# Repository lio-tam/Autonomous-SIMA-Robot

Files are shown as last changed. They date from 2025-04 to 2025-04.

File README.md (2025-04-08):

# Autonomer Roboter mit STM32
Dieses Projekt entstand im Rahmen meines Studiums an der RWTH Aachen. Ziel war es, einen Roboter zu bauen, der autonom einfache Bewegungen ausführt.

## Funktionen
- Eigenes Design der Steuerplatine mit KiCad
- Manuelle Bestückung & SMD-Löten
- Firmware in C für STM32
- Nutzung von Modm zum Flashen
- Projektplanung mit Gantt

## Verwendete Technologien
- STM32CubeIDE
- KiCad
- modm
- Logic Analyzer, CoolTerm

## Herausforderungen
- Fehlersuche bei Signalverlusten
- Austausch defekter Komponenten
- Zeitmanagement & Teamkoordination

## Medien
<div style="border:1px solid #ccc; border-radius:8px; padding:16px; margin:16px 0; box-shadow:2px 2px 6px rgba(0,0,0,0.1);">
  <h3 style="margin-top:12px;">Steuerplatine (Top View)</h3>
  <p>Die Oberseite der selbst entwickelten Steuerplatine – entworfen mit KiCad und per Hand bestückt.</p>
  driver-bild
</div>

<div style="border:1px solid #ccc; border-radius:8px; padding:16px; margin:16px 0; box-shadow:2px 2px 6px rgba(0,0,0,0.1);">
  <h3 style="margin-top:12px;">3D-Ansicht der Platine</h3>
  <p>Das mit KiCad erzeugte 3D-Modell zeigt die geplante Bestückung und Bauteilausrichtung.</p>
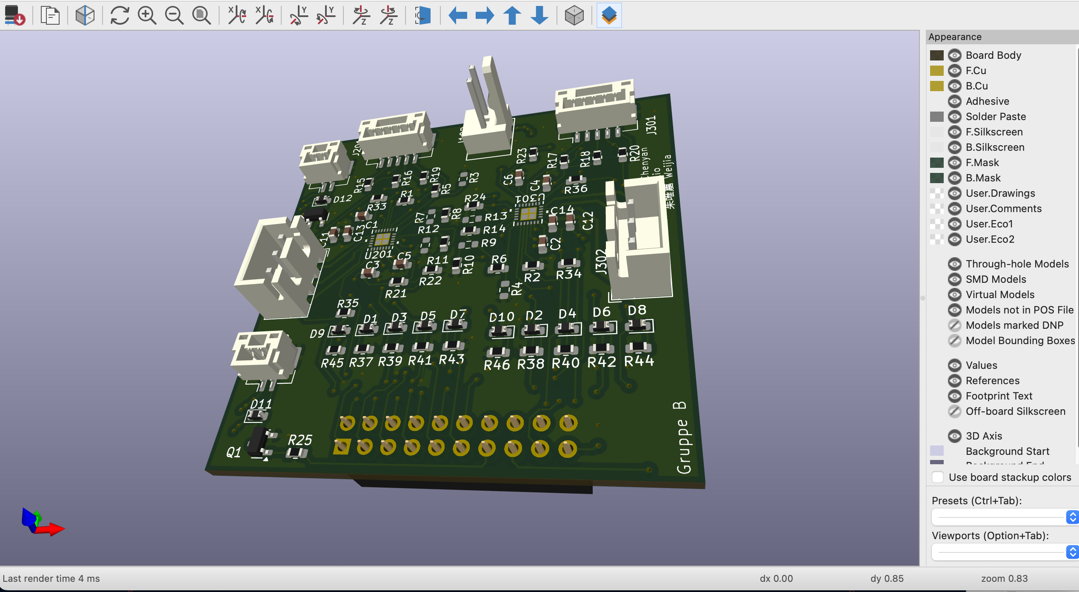
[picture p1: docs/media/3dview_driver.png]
3D-Ansicht
  
</div>

<div style="border:1px solid #ccc; border-radius:8px; padding:16px; margin:16px 0; box-shadow:2px 2px 6px rgba(0,0,0,0.1);">
  <h3 style="margin-top:12px;">Schaltplanansicht der Platine</h3>
  <p>Sie diente dazu, die Schaltungen zu planen und so anzuordnen, dass die Bauteile kompakt und effizient auf der Platine positioniert werden konnten.</p>
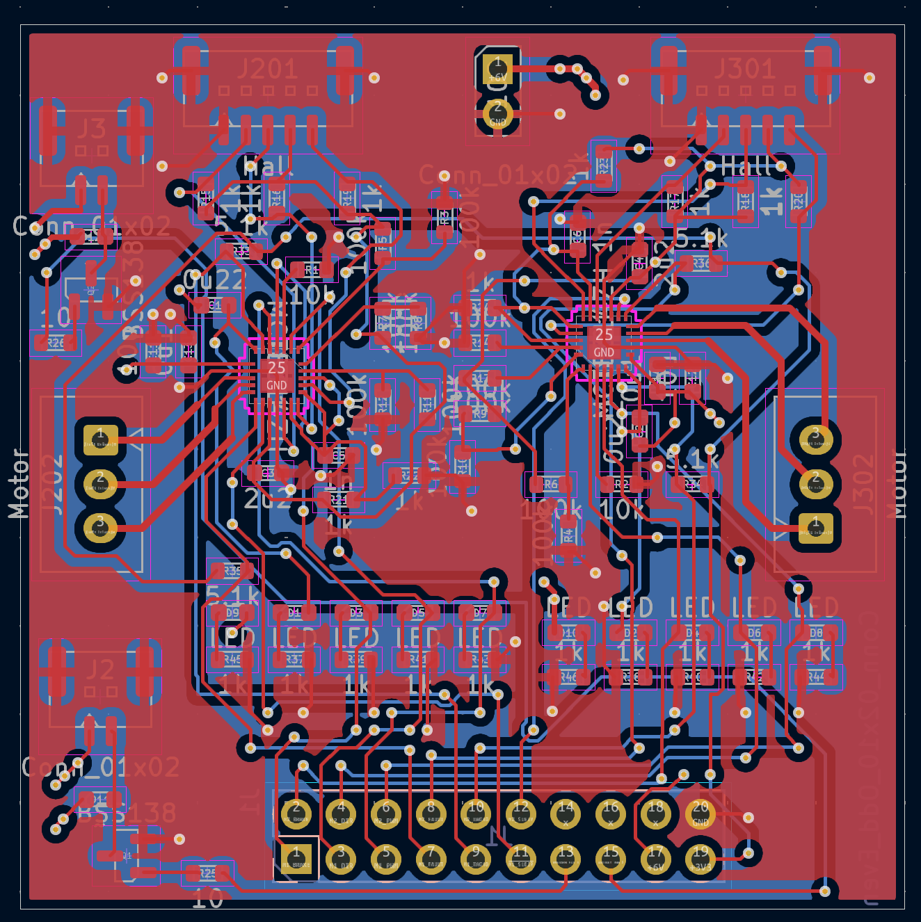
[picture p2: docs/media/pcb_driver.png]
Bestückte Platine
  
</div>

<div style="border:1px solid #ccc; border-radius:8px; padding:16px; margin:16px 0; box-shadow:2px 2px 6px rgba(0,0,0,0.1);">
  <h3 style="margin-top:12px;">Schaltplan – linker Teil</h3>
  <p>Ein Ausschnitt des Schaltplans mit Fokus auf die Spannungsversorgung und Mikrocontroller-Anbindung.</p>
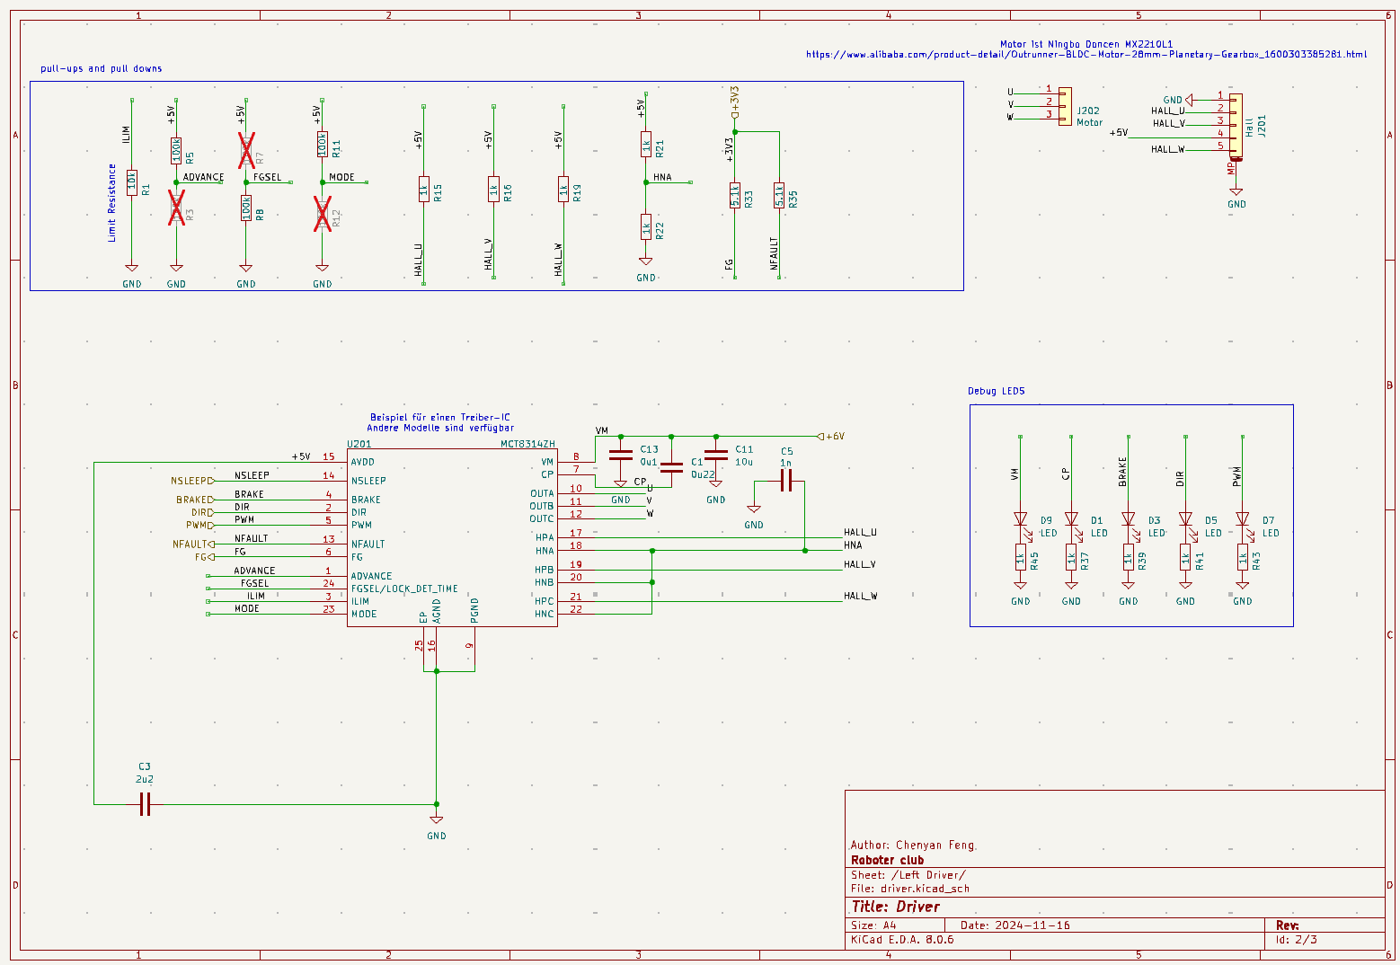
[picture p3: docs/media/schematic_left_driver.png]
Schaltplan (links)
  
</div>

<div style="border:1px solid #ccc; border-radius:8px; padding:16px; margin:16px 0; box-shadow:2px 2px 6px rgba(0,0,0,0.1);">
  <h3 style="margin-top:12px;">Firmware-Upload via SIMA</h3>
  <p>Flashing der Firmware über Modm – der Roboter wird mit neuer Software bespielt.</p>
  SIMA Flashing
</div>

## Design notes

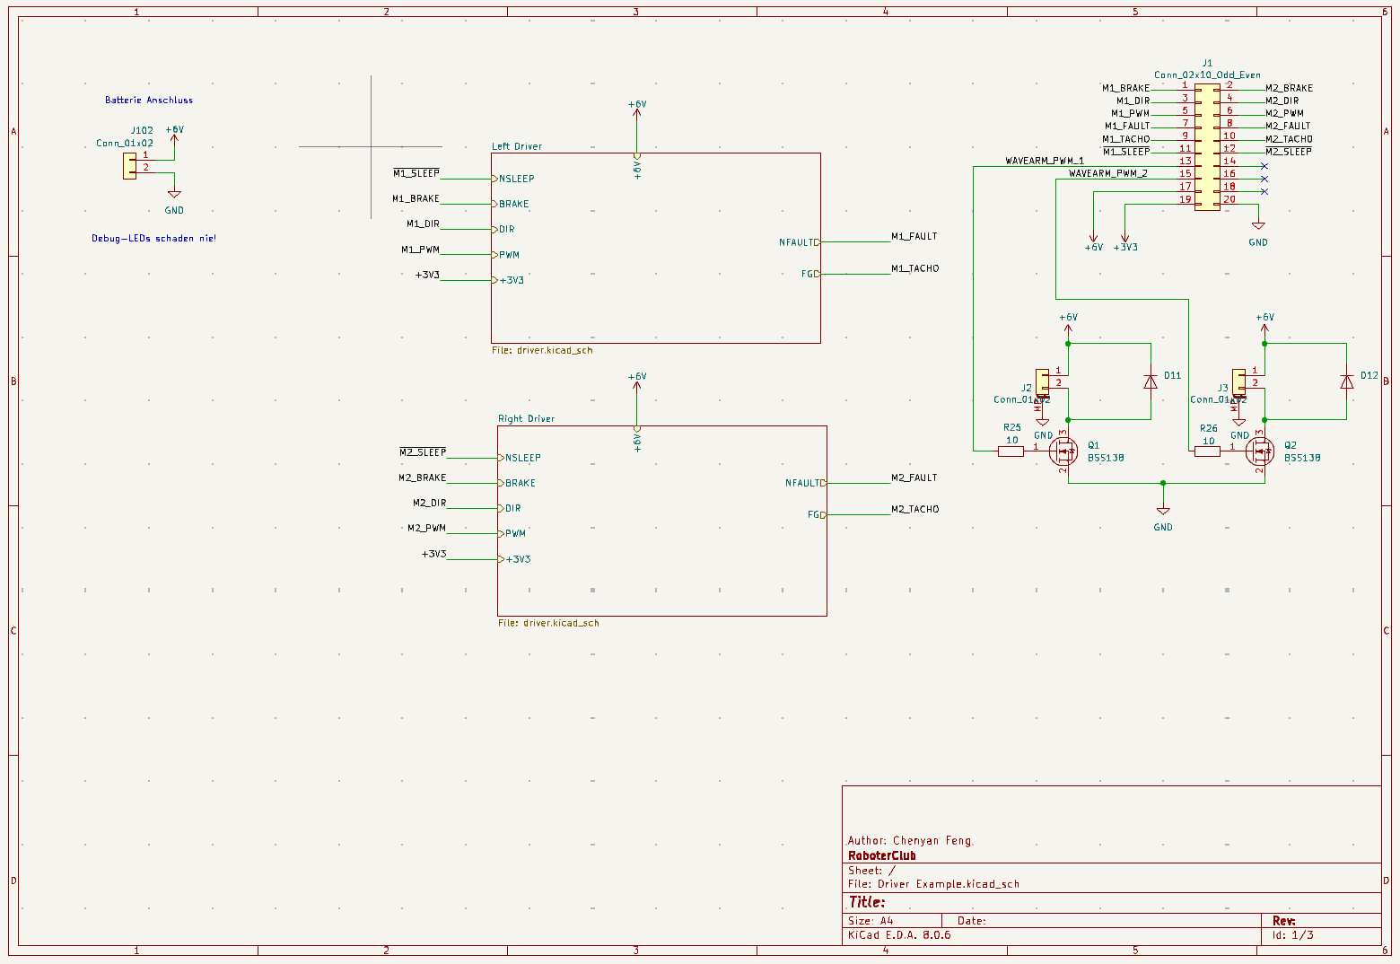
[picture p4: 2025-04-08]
docs/media/schematic_driver.png

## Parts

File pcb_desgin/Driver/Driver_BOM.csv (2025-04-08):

Reference | Value | Datasheet | Footprint | Name | Qty | Link | Preis | Gesamtpreis
C1;C2 | 0u22 | https://product.tdk.com/system/files/dam/doc/product/capacitor/ceramic/mlcc/catalog/mlcc_commercial_general_en.pdf | Capacitor_SMD:C_0603_1608Metric | C1608X5R1E224K080AA | 2 | https://www.digikey.de/de/products/detail/tdk-corporation/C1608X5R1E224K080AA/2093408 | 0,10 €
C3;C4 | 2u2 | https://mm.digikey.com/Volume0/opasdata/d220001/medias/docus/421/CL10A225KO8NNNC_Spec.pdf | Capacitor_SMD:C_0603_1608Metric | CL10A225KO8NNNC | 2 | https://www.digikey.de/de/products/detail/samsung-electro-mechanics/CL10A225KO8NNNC/3886698 | 0,08 €
C5;C6 | 1n | ~ | Capacitor_SMD:C_0603_1608Metric | CGA3E2X7R1H102K080DA | 2 | https://www.digikey.de/de/products/detail/tdk-corporation/CGA3E2X7R1H102K080DA/22106087 | 0,10 €
C11;C12 | 10u | ~ | Capacitor_SMD:C_0603_1608Metric | CL10A106KQ8NNNC | 2 | https://www.digikey.de/de/products/detail/samsung-electro-mechanics/CL10A106KQ8NNNC/3886696 | 0,10 €
C13;C14 | 0u1 | ~ | Capacitor_SMD:C_0603_1608Metric | TMK107BJ104KA-T | 2 | https://www.digikey.de/de/products/detail/taiyo-yuden/TMK107BJ104KA-T/930597 | 0,08 €
D1;D2;D3;D4;D5;D6;D7;D8;D9;D10 | LED | ~ | Diode_SMD:D_0603_1608Metric | 150060VS75000 | 10 | https://www.digikey.de/de/products/detail/w%C3%BCrth-elektronik/150060VS75000/4489906 | 0,13 €
D11;D12 | ~ | ~ | Diode_SMD:D_0603_1608Metric | VSKY20301608-G4-08 | 2 | https://www.digikey.de/de/products/detail/vishay-general-semiconductor-diodes-division/VSKY20301608-G4-08/6605119 | 0,48 €
J1 | Conn_02x10_Odd_Even | ~ | Connector_PinSocket_2.54mm:PinSocket_2x10_P2.54mm_Vertical | FHMD-DA020G1NBON-B | 1 | https://www.digikey.de/en/products/detail/superior-tech/FHMD-DA020G1NBON-B/16583446 | 0,69 €
J2;J3 | Conn_01x02 | ~ | Connector_JST:JST_GH_BM02B-GHS-TBT_1x02-1MP_P1.25mm_Vertical | BM02B-GHS-TBT | 2 | https://www.digikey.de/en/products/detail/jst-sales-america-inc/BM02B-GHS-TBT/807800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 | 0,31 €
J102 | Conn_01x02 | ~ | custom_footprints:2-Pin_PSK |  | 1
J201;J301 | Hall | ~ | Connector_JST:JST_GH_BM05B-GHS-TBT_1x05-1MP_P1.25mm_Vertical | BM05B-GHS-TBT | 2 | https://www.digikey.de/en/products/detail/jst-sales-america-inc/BM05B-GHS-TBT/807803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 | 0,39 €
J202;J302 | Motor | ~ | Connector_JST:JST_XH_B3B-XH-A_1x03_P2.50mm_Vertical | B3B-XH-A | 2 | https://www.digikey.de/en/products/detail/jst-sales-america-inc/B3B-XH-A(LF)(SN)/1651046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 | 0,12 €
Q1;Q2 | BSS138 | https://www.onsemi.com/pub/Collateral/BSS138-D.PDF | Package_TO_SOT_SMD:SOT-23 | BSS138 | 2 | https://www.digikey.de/de/products/detail/onsemi/BSS138/244210 | 0,26 €
R1;R2 | 10k | ~ | Resistor_SMD:R_0603_1608Metric | RMCF0603JT10K0 | 2 | https://www.digikey.de/de/products/detail/stackpole-electronics-inc/RMCF0603JT10K0/1758104 | 0,10 €
R3;R4;R7;R9;R12;R14 | 100k | ~ | Resistor_SMD:R_0603_1608Metric | ERJ-2RKF1003X | 6 | https://www.digikey.de/de/products/detail/panasonic-electronic-components/ERJ-2RKF1003X/192081 | 0,10 €
R5;R6;R8;R10;R11;R13 | 100k | ~ | Resistor_SMD:R_0603_1608Metric | ERJ-2RKF1003X | 6 | https://www.digikey.de/de/products/detail/panasonic-electronic-components/ERJ-2RKF1003X/192081 | 0,10 €
R15;R16;R17;R18;R19;R20;R21;R22;R23;R24;R37;R38;R39;R40;R41;R42;R43;R44;R45;R46 | 1k | ~ | Resistor_SMD:R_0603_1608Metric | ERJ-2RKF1001X | 20 | https://www.digikey.de/de/products/detail/panasonic-electronic-components/ERJ-2RKF1001X/79729 | 0,10 €
R25;R26 | 10 | ~ | Resistor_SMD:R_0603_1608Metric | ERJ-2RKF10R0X | 2 | https://www.digikey.de/de/products/detail/panasonic-electronic-components/ERJ-2RKF10R0X/192072 | 0,10 €
R33;R34;R35;R36 | 5.1k | ~ | Resistor_SMD:R_0603_1608Metric | ERA-2AEB512X | 4 | https://www.digikey.de/de/products/detail/panasonic-electronic-components/ERA-2AEB512X/1706022 | 0,17 €
U201;U301 | MCT8314ZH | https://www.ti.com/product/MCT8314Z | custom_footprints:WQFN24_RRW_TEX_new |  | 2

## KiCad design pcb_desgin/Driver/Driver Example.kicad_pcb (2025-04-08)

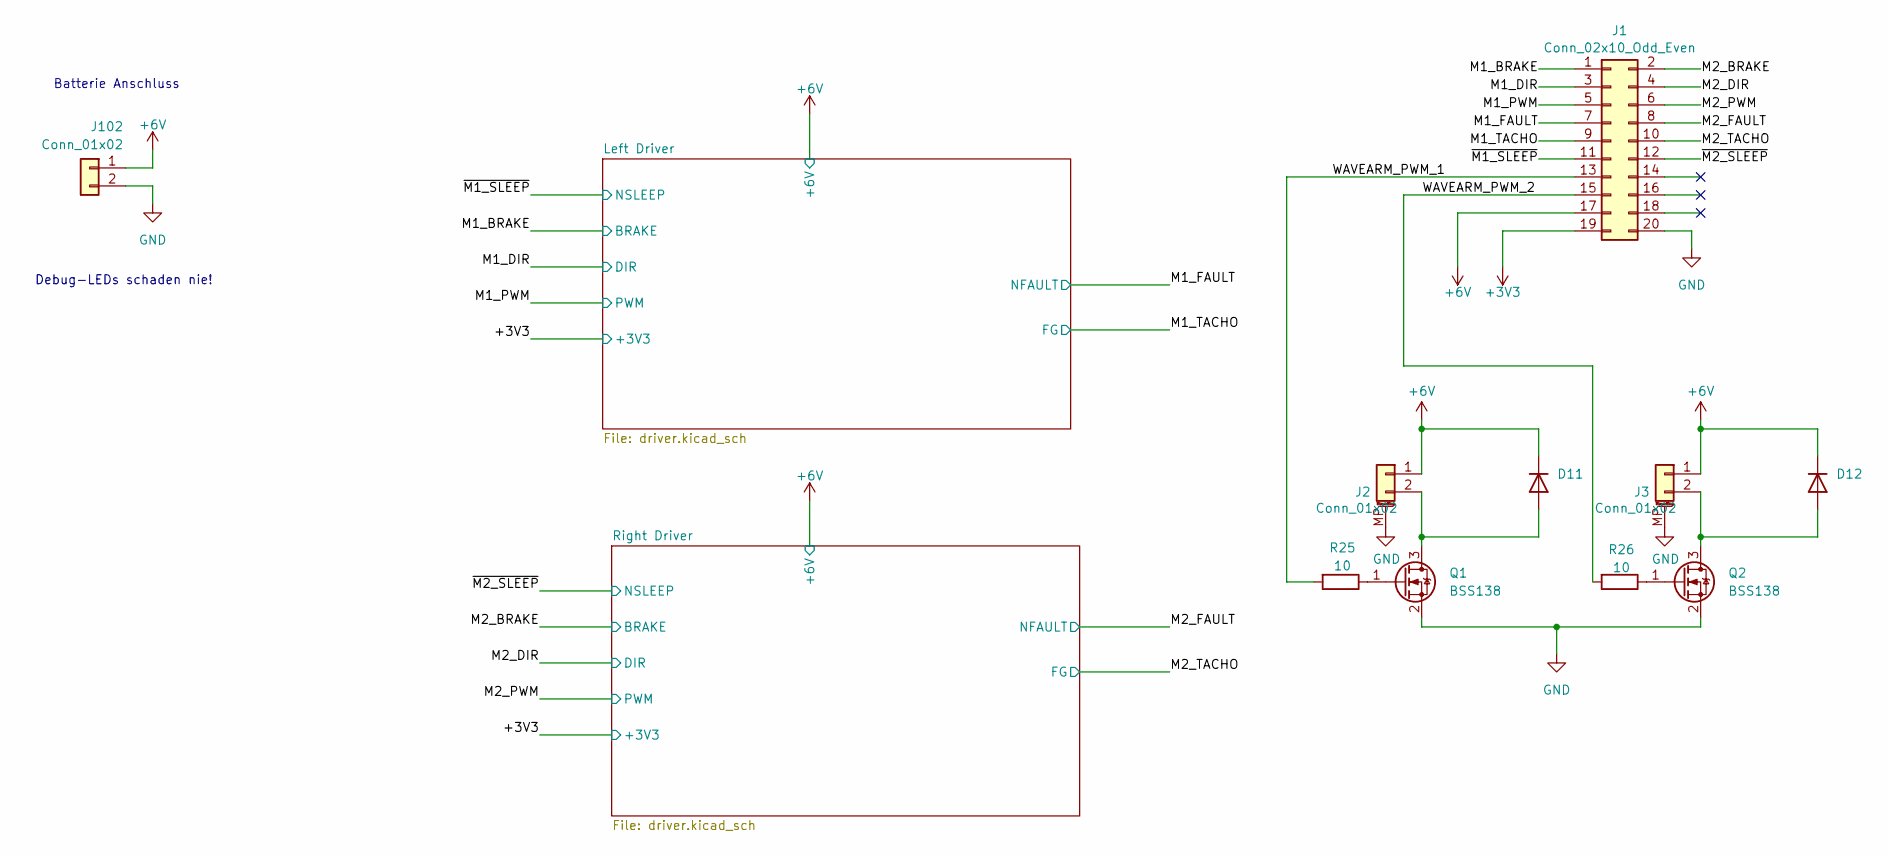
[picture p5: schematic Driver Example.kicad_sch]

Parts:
D11, D12: D_0603_1608Metric
J1: Conn_02x10_Odd_Even; PinSocket_2x10_P2.54mm_Vertical
J2, J3: Conn_01x02; JST_GH_BM02B-GHS-TBT_1x02-1MP_P1.25mm_Vertical
J102: Conn_01x02; 2-Pin_PSK
Q1, Q2: BSS138; SOT-23
R25, R26: 10; R_0603_1608Metric

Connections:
+3V3: J1.19; also elsewhere on the board
+6V: D11.1 (K), D12.1 (K), J1.17, J2.1, J3.1, J102.1; also elsewhere on the board
/M1_BRAKE: J1.1; also elsewhere on the board
/M1_DIR: J1.3; also elsewhere on the board
/M1_FAULT: J1.7; also elsewhere on the board
/M1_PWM: J1.5; also elsewhere on the board
/M1_TACHO: J1.9; also elsewhere on the board
/M2_BRAKE: J1.2; also elsewhere on the board
/M2_DIR: J1.4; also elsewhere on the board
/M2_FAULT: J1.8; also elsewhere on the board
/M2_PWM: J1.6; also elsewhere on the board
/M2_TACHO: J1.10; also elsewhere on the board
/WAVEARM_PWM_1: J1.13, R25.2
/WAVEARM_PWM_2: J1.15, R26.2
/~M1_SLEEP: J1.11; also elsewhere on the board
/~M2_SLEEP: J1.12; also elsewhere on the board
GND: J1.20, J2.MP (MountPin), J3.MP (MountPin), J102.2, Q1.2 (S), Q2.2 (S); also elsewhere on the board
unnamed: D11.2 (A), J2.2, Q1.3 (D)
unnamed: D12.2 (A), J3.2, Q2.3 (D)
unnamed: Q1.1 (G), R25.1
unnamed: Q2.1 (G), R26.1

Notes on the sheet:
Debug-LEDs schaden nie!
Batterie Anschluss

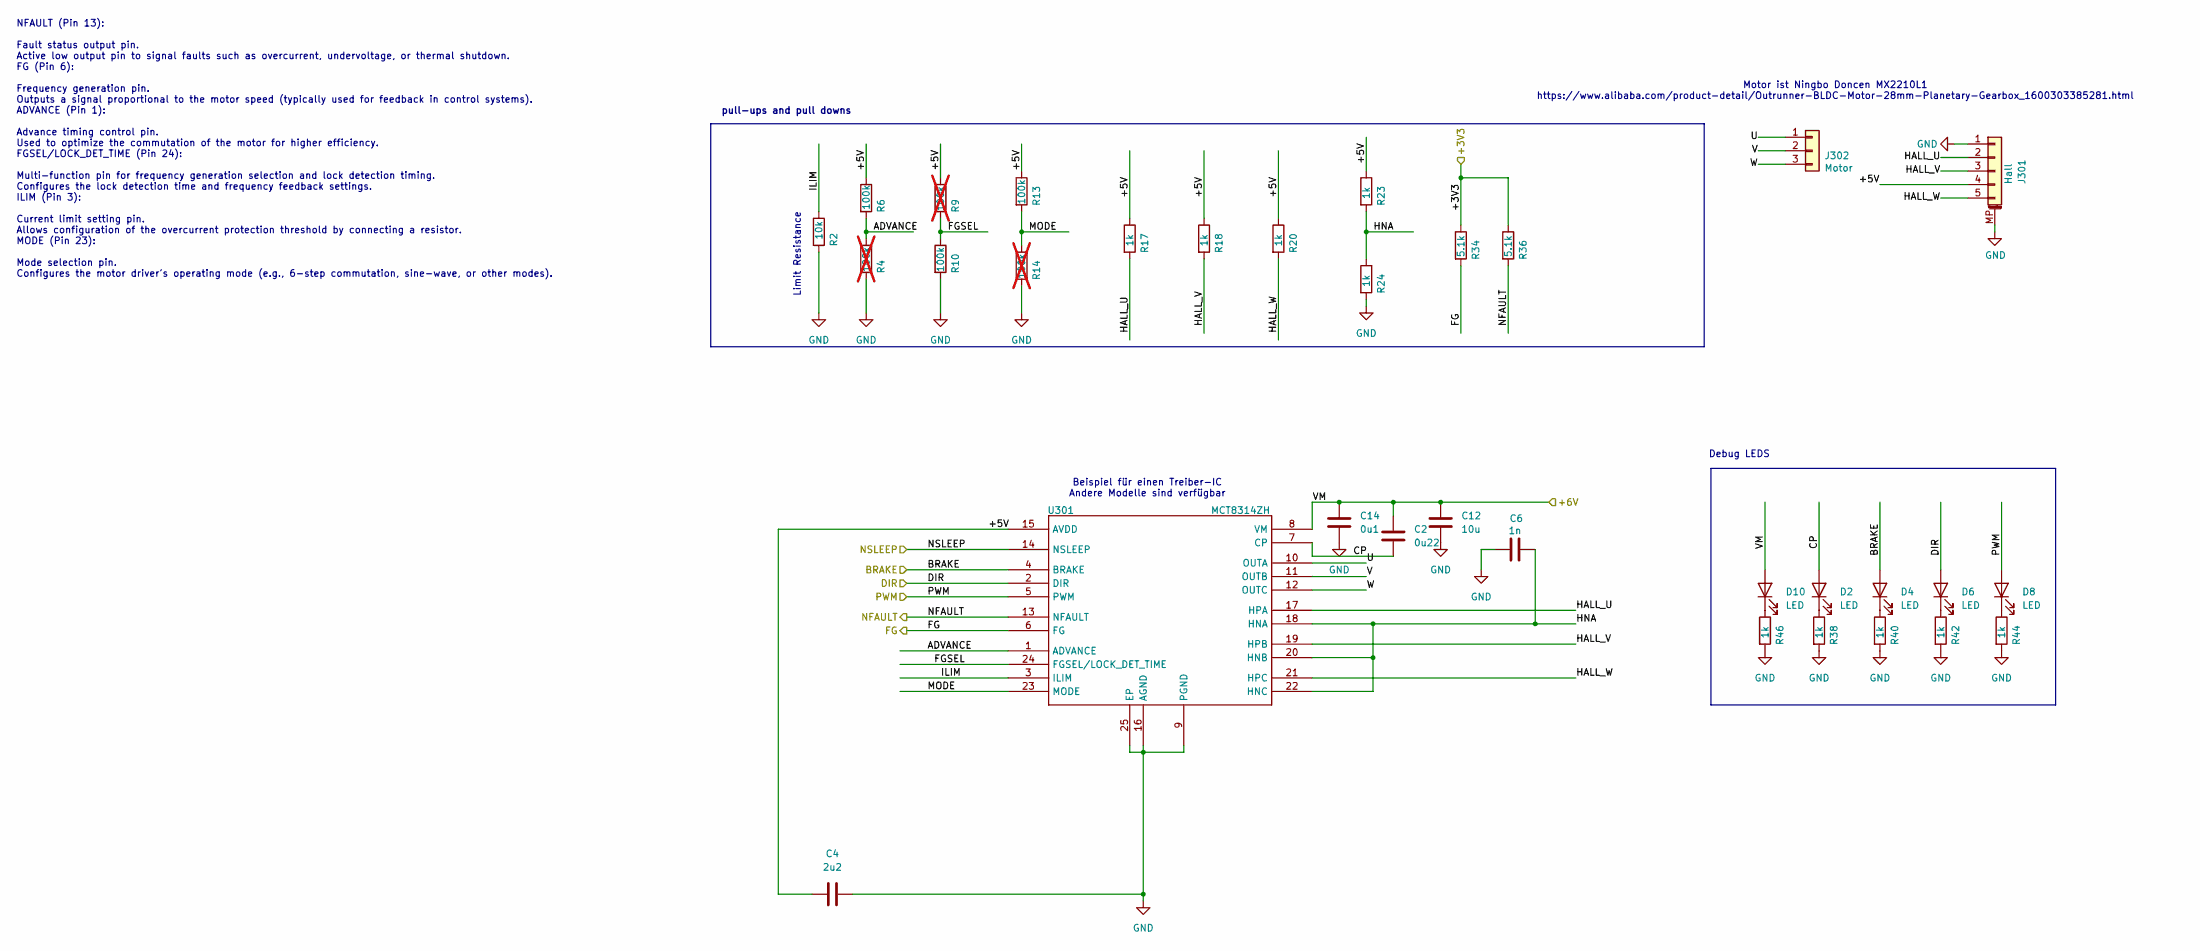
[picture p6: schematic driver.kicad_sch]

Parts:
C2: 0u22; C_0603_1608Metric
C4: 2u2; C_0603_1608Metric
C6: 1n; C_0603_1608Metric
C12: 10u; C_0603_1608Metric
C14: 0u1; C_0603_1608Metric
D2, D4, D6, D8, D10: LED; D_0603_1608Metric
J301: Hall; JST_GH_BM05B-GHS-TBT_1x05-1MP_P1.25mm_Vertical
J302: Motor; JST_XH_B3B-XH-A_1x03_P2.50mm_Vertical
R2: 10k; R_0603_1608Metric
R4, R9, R14: 100k; R_0603_1608Metric; not fitted
R6, R10, R13: 100k; R_0603_1608Metric
R17, R18, R20, R23, R24, R38, R40, R42, R44, R46: 1k; R_0603_1608Metric
R34, R36: 5.1k; R_0603_1608Metric
U301: MCT8314ZH; WQFN24_RRW_TEX_new

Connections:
+3V3: R34.1, R36.1; also elsewhere on the board
+6V: C2.2, C12.2, C14.2, D10.2 (A), U301.8 (VM); also elsewhere on the board
/M2_BRAKE: D4.2 (A), U301.4 (BRAKE); also elsewhere on the board
/M2_DIR: D6.2 (A), U301.2 (DIR); also elsewhere on the board
/M2_FAULT: R36.2, U301.13 (NFAULT); also elsewhere on the board
/M2_PWM: D8.2 (A), U301.5 (PWM); also elsewhere on the board
/M2_TACHO: R34.2, U301.6 (FG); also elsewhere on the board
/Right Driver/+5V: C4.1, J301.4, R6.1, R9.1, R13.1, R17.1, R18.1, R20.1, R23.1, U301.15 (AVDD)
/Right Driver/ADVANCE: R4.1, R6.2, U301.1 (ADVANCE)
/Right Driver/CP: C2.1, D2.2 (A), U301.7 (CP)
/Right Driver/FGSEL: R9.2, R10.1, U301.24 (FGSEL/LOCK_DET_TIME)
/Right Driver/HALL_U: J301.2, R17.2, U301.17 (HPA)
/Right Driver/HALL_V: J301.3, R18.2, U301.19 (HPB)
/Right Driver/HALL_W: J301.5, R20.2, U301.21 (HPC)
/Right Driver/HNA: C6.1, R23.2, R24.1, U301.18 (HNA), U301.20 (HNB), U301.22 (HNC)
/Right Driver/ILIM: R2.1, U301.3 (ILIM)
/Right Driver/MODE: R13.2, R14.1, U301.23 (MODE)
/Right Driver/U: J302.1, U301.10 (OUTA)
/Right Driver/V: J302.2, U301.11 (OUTB)
/Right Driver/W: J302.3, U301.12 (OUTC)
/~M2_SLEEP: U301.14 (NSLEEP); also elsewhere on the board
GND: C4.2, C6.2, C12.1, C14.1, J301.1, J301.MP (MountPin), R2.2, R4.2, R10.2, R14.2, R24.2, R38.2, R40.2, R42.2, R44.2, R46.2, U301.9 (PGND), U301.16 (AGND), U301.25 (EP); also elsewhere on the board
unnamed: D2.1 (K), R38.1
unnamed: D4.1 (K), R40.1
unnamed: D6.1 (K), R42.1
unnamed: D8.1 (K), R44.1
unnamed: D10.1 (K), R46.1

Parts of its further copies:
C1: 0u22; C_0603_1608Metric
C3: 2u2; C_0603_1608Metric
C5: 1n; C_0603_1608Metric
C11: 10u; C_0603_1608Metric
C13: 0u1; C_0603_1608Metric
D1, D3, D5, D7, D9: LED; D_0603_1608Metric
J201: Hall; JST_GH_BM05B-GHS-TBT_1x05-1MP_P1.25mm_Vertical
J202: Motor; JST_XH_B3B-XH-A_1x03_P2.50mm_Vertical
R1: 10k; R_0603_1608Metric
R3, R7, R12: 100k; R_0603_1608Metric; not fitted
R5, R8, R11: 100k; R_0603_1608Metric
R15, R16, R19, R21, R22, R37, R39, R41, R43, R45: 1k; R_0603_1608Metric
R33, R35: 5.1k; R_0603_1608Metric
U201: MCT8314ZH; WQFN24_RRW_TEX_new

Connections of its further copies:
+3V3: R33.1, R35.1; also elsewhere on the board
+6V: C1.2, C11.2, C13.2, D9.2 (A), U201.8 (VM); also elsewhere on the board
/Left Driver/+5V: C3.1, J201.4, R5.1, R7.1, R11.1, R15.1, R16.1, R19.1, R21.1, U201.15 (AVDD)
/Left Driver/ADVANCE: R3.1, R5.2, U201.1 (ADVANCE)
/Left Driver/CP: C1.1, D1.2 (A), U201.7 (CP)
/Left Driver/FGSEL: R7.2, R8.1, U201.24 (FGSEL/LOCK_DET_TIME)
/Left Driver/HALL_U: J201.2, R15.2, U201.17 (HPA)
/Left Driver/HALL_V: J201.3, R16.2, U201.19 (HPB)
/Left Driver/HALL_W: J201.5, R19.2, U201.21 (HPC)
/Left Driver/HNA: C5.1, R21.2, R22.1, U201.18 (HNA), U201.20 (HNB), U201.22 (HNC)
/Left Driver/ILIM: R1.1, U201.3 (ILIM)
/Left Driver/MODE: R11.2, R12.1, U201.23 (MODE)
/Left Driver/U: J202.1, U201.10 (OUTA)
/Left Driver/V: J202.2, U201.11 (OUTB)
/Left Driver/W: J202.3, U201.12 (OUTC)
/M1_BRAKE: D3.2 (A), U201.4 (BRAKE); also elsewhere on the board
/M1_DIR: D5.2 (A), U201.2 (DIR); also elsewhere on the board
/M1_FAULT: R35.2, U201.13 (NFAULT); also elsewhere on the board
/M1_PWM: D7.2 (A), U201.5 (PWM); also elsewhere on the board
/M1_TACHO: R33.2, U201.6 (FG); also elsewhere on the board
/~M1_SLEEP: U201.14 (NSLEEP); also elsewhere on the board
GND: C3.2, C5.2, C11.1, C13.1, J201.1, J201.MP (MountPin), R1.2, R3.2, R8.2, R12.2, R22.2, R37.2, R39.2, R41.2, R43.2, R45.2, U201.9 (PGND), U201.16 (AGND), U201.25 (EP); also elsewhere on the board
unnamed: D1.1 (K), R37.1
unnamed: D3.1 (K), R39.1
unnamed: D5.1 (K), R41.1
unnamed: D7.1 (K), R43.1
unnamed: D9.1 (K), R45.1

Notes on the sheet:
NFAULT (Pin 13): Fault status output pin. Active low output pin to signal faults such as overcurrent, undervoltage, or thermal shutdown. FG (Pin 6): Frequency generation pin. Outputs a signal proportional to the motor speed (typically used for feedback in control systems). ADVANCE (Pin 1): Advance 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
Debug LEDS
Motor ist Ningbo Doncen MX2210L1 https://www.alibaba.com/product-detail/Outrunner-BLDC-Motor-28mm-Planetary-Gearbox_1600303385281.html
Beispiel für einen Treiber-IC Andere Modelle sind verfügbar
pull-ups and pull downs
Limit Resistance

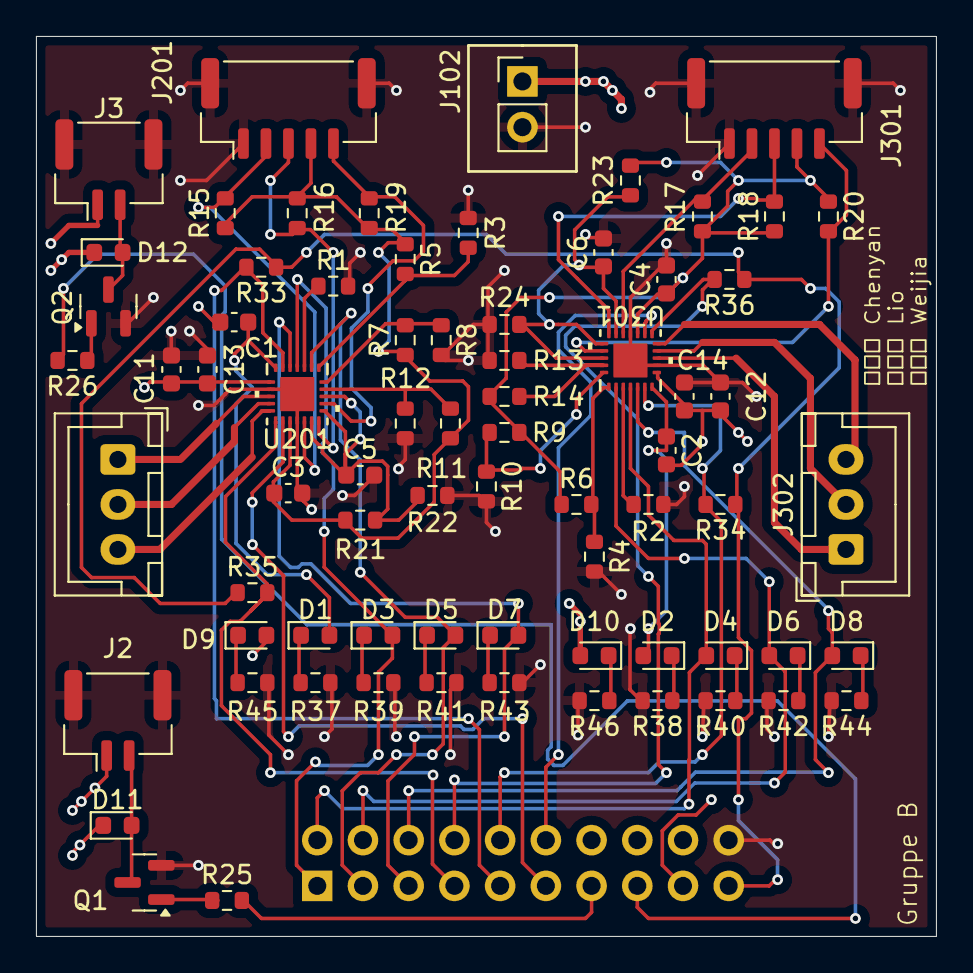
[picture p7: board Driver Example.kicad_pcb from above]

Board: 4 copper layers, 50.0 x 50.0 mm, 74 parts (1 on the bottom side), 57 nets.

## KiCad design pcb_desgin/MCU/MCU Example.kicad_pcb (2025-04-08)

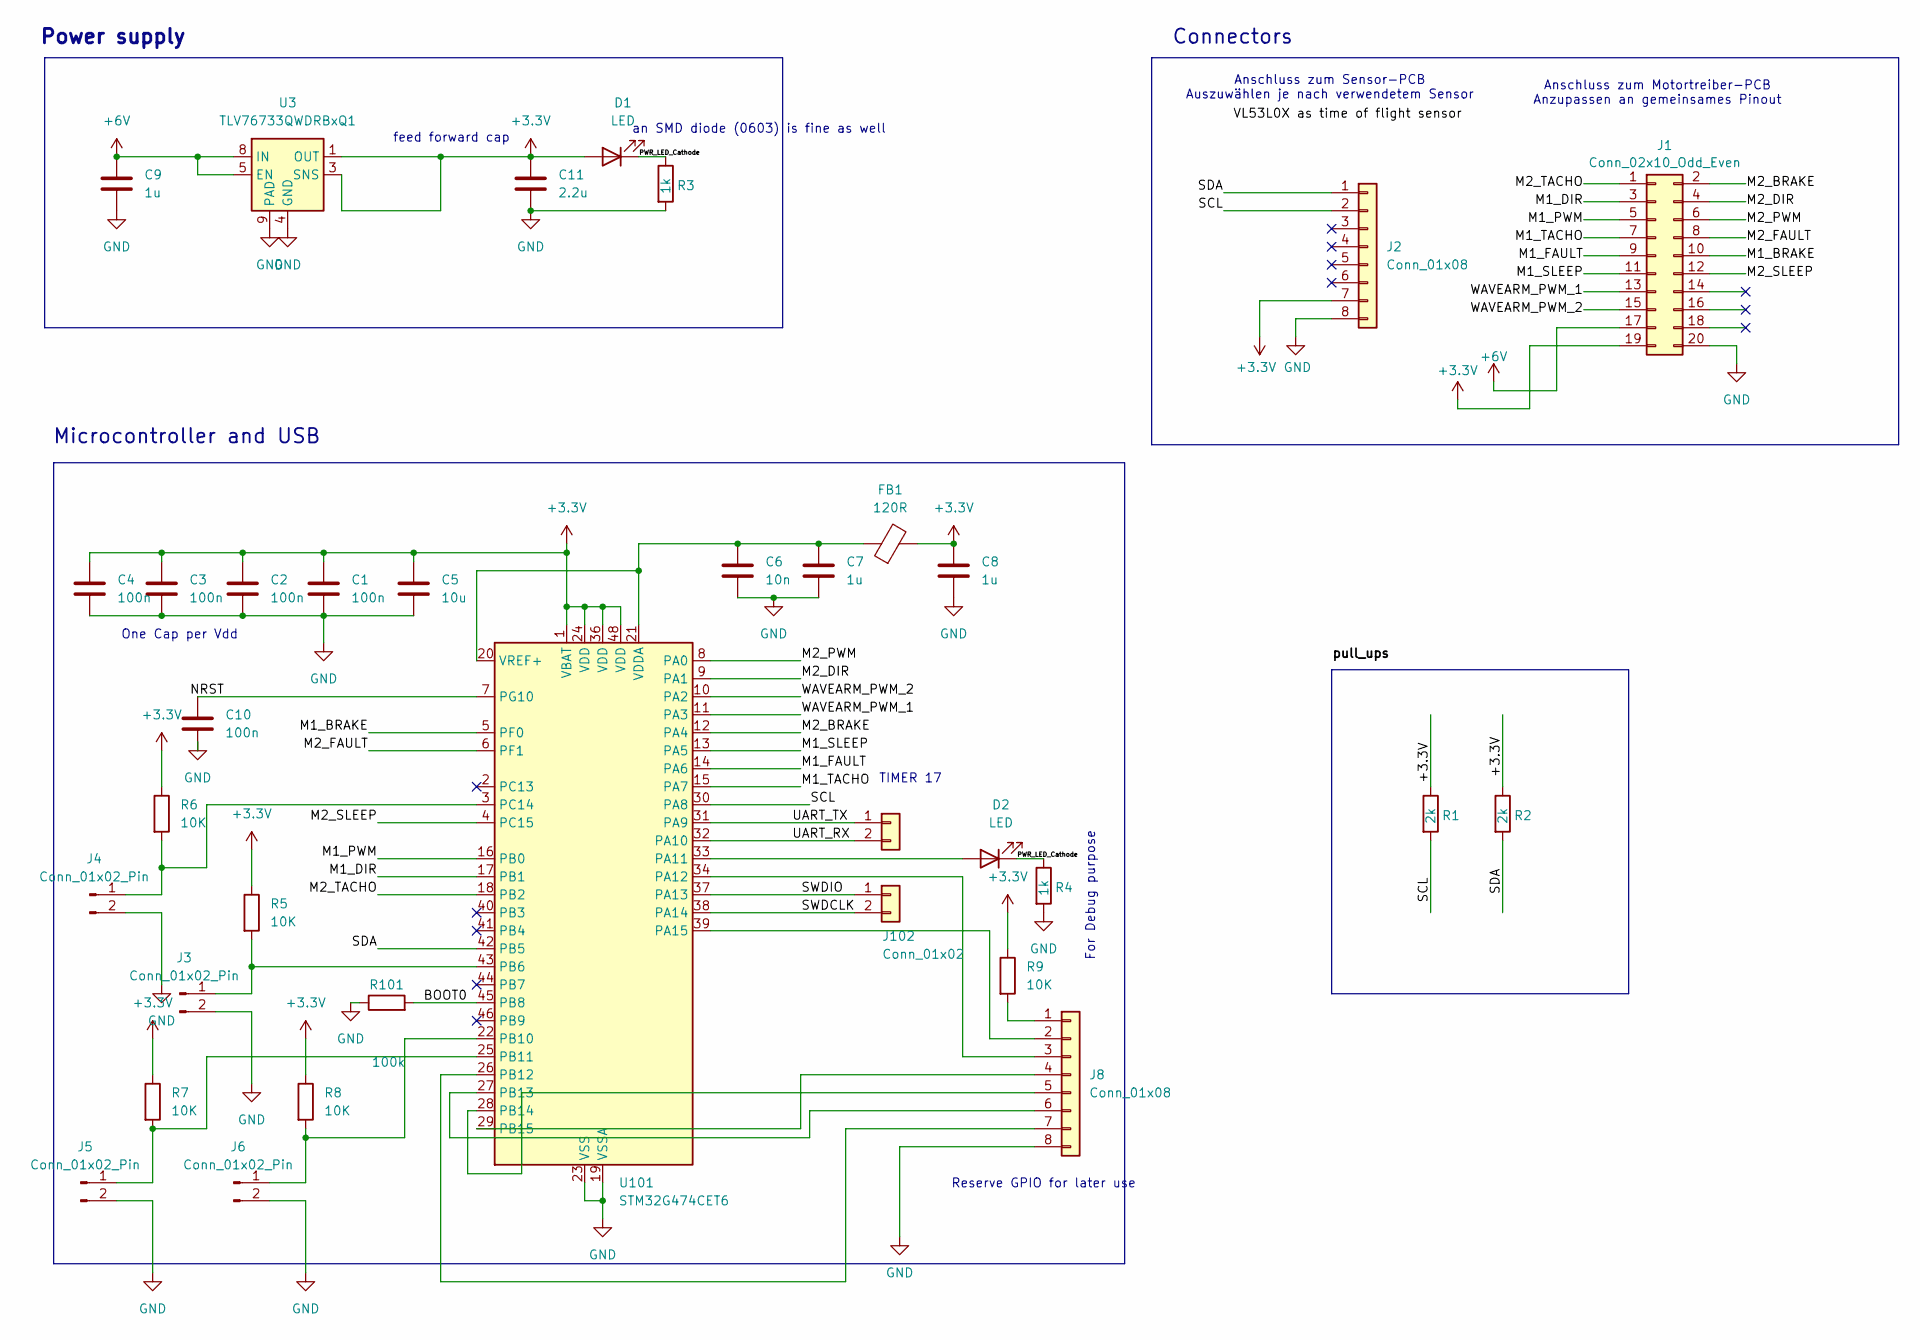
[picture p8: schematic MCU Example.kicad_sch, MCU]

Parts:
C1, C2, C3, C4, C10: 100n; C_0603_1608Metric
C5: 10u; C_0603_1608Metric
C6: 10n; C_0603_1608Metric
C7, C8, C9: 1u; C_0603_1608Metric
C11: 2.2u; C_0603_1608Metric
D1, D2: LED; D_0603_1608Metric
FB1: 120R; L_0603_1608Metric
J1: Conn_02x10_Odd_Even; PinHeader_2x10_P2.54mm_Horizontal
J2: Conn_01x08; PinHeader_1x08_P1.00mm_Horizontal
J3, J4, J5, J6: Conn_01x02_Pin; PinHeader_1x02_P1.00mm_Vertical
J8: Conn_01x08; PinHeader_1x08_P1.00mm_Vertical
J101, J102: Conn_01x02; JST_GH_BM02B-GHS-TBT_1x02-1MP_P1.25mm_Vertical
R1, R2: 2k; R_0603_1608Metric
R3, R4: 1k; R_0603_1608Metric
R5, R6, R7, R8, R9: 10K; R_0603_1608Metric
R101: 100k; R_0603_1608Metric
U3: TLV76733QWDRBxQ1; VSON-8-1EP_3x3mm_P0.65mm_EP1.65x2.4mm
U101: STM32G474CET6; LQFP-48_7x7mm_P0.5mm

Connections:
+3.3V: C1.1, C2.1, C3.1, C4.1, C5.1, C8.1, C11.1, D1.2 (A), FB1.2, J1.19, J2.7, R1.1, R2.1, R5.1, R6.1, R7.1, R8.1, R9.1, U3.1 (OUT), U3.3 (SNS), U101.1 (VBAT), U101.24 (VDD), U101.36 (VDD), U101.48 (VDD)
+6V: C9.1, J1.17, U3.5 (EN), U3.8 (IN)
/BOOT0: R101.2, U101.45 (PB8)
/M1_BRAKE: J1.10, U101.5 (PF0)
/M1_DIR: J1.3, U101.17 (PB1)
/M1_FAULT: J1.9, U101.14 (PA6)
/M1_PWM: J1.5, U101.16 (PB0)
/M1_SLEEP: J1.11, U101.13 (PA5)
/M1_TACHO: J1.7, U101.15 (PA7)
/M2_BRAKE: J1.2, U101.12 (PA4)
/M2_DIR: J1.4, U101.9 (PA1)
/M2_FAULT: J1.8, U101.6 (PF1)
/M2_PWM: J1.6, U101.8 (PA0)
/M2_SLEEP: J1.12, U101.4 (PC15)
/M2_TACHO: J1.1, U101.18 (PB2)
/NRST: C10.1, U101.7 (PG10)
/PWR_LED_Cathode: D1.1 (K), D2.1 (K), R3.1, R4.1
/SCL: J2.2, R1.2, U101.30 (PA8)
/SDA: J2.1, R2.2, U101.42 (PB5)
/SWDCLK: J102.2, U101.38 (PA14)
/SWDIO: J102.1, U101.37 (PA13)
/UART_RX: J101.2, U101.32 (PA10)
/UART_TX: J101.1, U101.31 (PA9)
/WAVEARM_PWM_1: J1.13, U101.11 (PA3)
/WAVEARM_PWM_2: J1.15, U101.10 (PA2)
GND: C1.2, C2.2, C3.2, C4.2, C5.2, C6.2, C7.2, C8.2, C9.2, C10.2, C11.2, J1.20, J2.8, J3.2, J4.2, J5.2, J6.2, J8.8, R3.2, R4.2, R101.1, U3.4 (GND), U3.6 (GND), U3.9 (PAD), U101.19 (VSSA), U101.23 (VSS), U101.35 (VSS), U101.47 (VSS)
unnamed: D2.2 (A), U101.33 (PA11)
unnamed: J3.1, R5.2, U101.43 (PB6)
unnamed: J4.1, R6.2, U101.3 (PC14)
unnamed: J5.1, R7.2, U101.25 (PB11)
unnamed: J6.1, R8.2, U101.22 (PB10)
unnamed: J8.1, R9.2
unnamed: J8.2, U101.39 (PA15)
unnamed: J8.3, U101.34 (PA12)
unnamed: J8.4, U101.29 (PB15)
unnamed: J8.5, U101.28 (PB14)
unnamed: J8.6, U101.27 (PB13)
unnamed: J8.7, U101.26 (PB12)
unnamed: C6.1, C7.1, FB1.1, U101.20 (VREF+), U101.21 (VDDA)

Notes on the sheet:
Connectors
One Cap per Vdd
TIMER 17
feed forward cap
Anschluss zum Motortreiber-PCB Anzupassen an gemeinsames Pinout
an SMD diode (0603) is fine as well
Microcontroller and USB
Reserve GPIO for later use
Anschluss zum Sensor-PCB Auszuwählen je nach verwendetem Sensor
For Debug purpose
Power supply

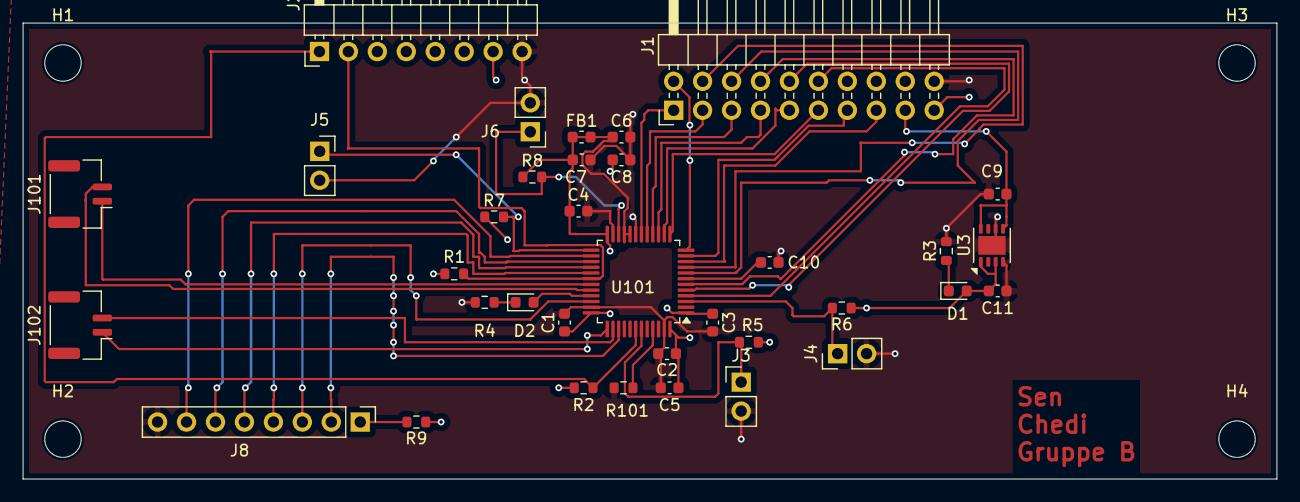
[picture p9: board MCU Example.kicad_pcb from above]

Board: 4 copper layers, 110.0 x 40.0 mm, 39 parts (0 on the bottom side), 39 nets.

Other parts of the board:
H1, H2, H3, H4: MountingHole; MountingHole_3.2mm_M3

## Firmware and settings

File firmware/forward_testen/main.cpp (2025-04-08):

#include "hardware.hpp"
#include <modm/architecture/interface/delay.hpp>
#include <modm/debug/logger.hpp>

using namespace Board;

/**
 * @brief Drives the motor at a given speed percentage.
 *
 * Sets the PWM duty cycle for the motor channels.
 */
void driveForward(uint16_t speedPercent)
{
    if (speedPercent > 100) {
        speedPercent = 100;
    }

    // (Assumes that the Direction pins are set by the caller.)
    uint16_t duty1 = (MotorTimer3::getOverflow() * speedPercent) / 100;
    uint16_t duty2 = (MotorTimer2::getOverflow() * speedPercent) / 100;

    MotorTimer3::configureOutputChannel<GpioB0::Ch3>(
        MotorTimer3::OutputCompareMode::Pwm, duty1);
    MotorTimer2::configureOutputChannel<GpioA0::Ch1>(
        MotorTimer2::OutputCompareMode::Pwm, duty2);

    MotorTimer3::applyAndReset();
    MotorTimer3::start();
    MotorTimer2::applyAndReset();
    MotorTimer2::start();
}

/**
 * @brief Logs PWM settings.
 *
 * Displays key parameters (here, the overflow values) so you can verify
 * that the PWM is configured as expected.
 */
void logPwmSettings()
{
    uint16_t overflow1 = MotorTimer3::getOverflow();
    uint16_t overflow2 = MotorTimer2::getOverflow();

    MODM_LOG_INFO << "PWM Settings:" << modm::endl;
    MODM_LOG_INFO << "  MotorTimer3 overflow = " << overflow1 << modm::endl;
    MODM_LOG_INFO << "  MotorTimer2 overflow = " << overflow2 << modm::endl;
    modm::delay_ms(100);
}

/**
 * @brief Drives the motor with a full (or zero) duty cycle.
 *
 * Useful for verifying that the PWM output itself is working.
 *
 * @param fullOn If true, sets duty cycle to 100%; if false, sets to 0%.
 */
void driveAtFullDuty(bool fullOn = true)
{
    uint16_t duty = fullOn ? MotorTimer3::getOverflow() : 0;
    MODM_LOG_INFO << "Setting PWM duty to " << (fullOn ? "100%" : "0%")
                  << " (" << duty << ")" << modm::endl;
    modm::delay_ms(100);

    MotorTimer3::configureOutputChannel<GpioB0::Ch3>(
        MotorTimer3::OutputCompareMode::Pwm, duty);
    MotorTimer2::configureOutputChannel<GpioA0::Ch1>(
        MotorTimer2::OutputCompareMode::Pwm, duty);

    MotorTimer3::applyAndReset();
    MotorTimer2::applyAndReset();
}

/**
 * @brief Toggles the PWM pin as a digital output.
 *
 * Temporarily reconfigures the PWM pin (assumed to be GpioB0) as a digital output and toggles it.
 * After testing, restores PWM functionality.
 */
void testPwmPinToggle()
{
    MODM_LOG_INFO << "Starting PWM pin toggle test..." << modm::endl;
    modm::delay_ms(100);

    // Temporarily disable PWM on M1_Pwm and reconfigure it as a standard output.
    M1_Pwm::setOutput();

    // Toggle the pin 10 times.
    for (int i = 0; i < 10; ++i) {
        M1_Pwm::toggle();
        MODM_LOG_INFO << "  Toggling PWM pin (" << (i + 1) << "/10)" << modm::endl;
        modm::delay_ms(500);
    }

    // Restore PWM functionality.
    MotorTimer3::connect<GpioB0::Ch3>();
    MotorTimer3::start();

    MODM_LOG_INFO << "PWM pin toggle test complete." << modm::endl;
    modm::delay_ms(100);
}

/**
 * @brief Tests various enable combinations while allowing manual rotation.
 *
 * This function cycles through four specific combinations:
 *
 * 1. Normal Operation: nSLEEP = HIGH, BRAKE = LOW, DIR = LOW.
 * 2. Reverse Operation: nSLEEP = HIGH, BRAKE = LOW, DIR = HIGH.
 * 3. Brake Active: nSLEEP = HIGH, BRAKE = HIGH, DIR = LOW.
 * 4. Sleep Mode: nSLEEP = LOW, BRAKE = LOW, DIR = LOW.
 *
 * For each combination, the motor is driven at a preset PWM duty cycle (75%)
 * and the program waits 10 seconds to allow you to manually rotate the wheel
 * to see if the motor begins commutating.
 */
void testEnableModes(uint16_t speedPercent)
{
    // const uint16_t speedPercent = 75;
    const int testDuration_ms = 10000;  // 10 seconds per configuration

    // Test 1: Normal Operation
    MODM_LOG_INFO << "01" << modm::endl; // "Test 1: Normal Operation (nSLEEP=HIGH, BRAKE=LOW, DIR=LOW)"
    M1_Sleep::setOutput(true);  // nSLEEP high: driver active.
    M2_Sleep::setOutput(true);
    M1_Brake::setOutput(false); // BRAKE low: normal operation.
    M2_Brake::setOutput(false);
    M1_Dir::setOutput(false);   // DIR low: choose clockwise (for example).
    M2_Dir::setOutput(false);
    driveForward(speedPercent);
    MODM_LOG_INFO << "cw" << modm::endl; // "Rotate wheel manually (clockwise) now."
    modm::delay_ms(testDuration_ms);

    // Test 2: Reverse Operation
    MODM_LOG_INFO << "02" << modm::endl;  // "Test 2: Reverse Operation (nSLEEP=HIGH, BRAKE=LOW, DIR=HIGH)"
    M1_Sleep::setOutput(true);
    M2_Sleep::setOutput(true);
    M1_Brake::setOutput(false);
    M2_Brake::setOutput(false);
    M1_Dir::setOutput(true);   // DIR high: reverse rotation.
    M2_Dir::setOutput(true);
    driveForward(speedPercent);
    MODM_LOG_INFO << "cc" << modm::endl; //  "Rotate wheel manually (counterclockwise) now."
    modm::delay_ms(testDuration_ms);

    // Test 3: Brake Active
    MODM_LOG_INFO << "03" << modm::endl; // "Test 3: Brake Active (nSLEEP=HIGH, BRAKE=HIGH, DIR=LOW)"
    M1_Sleep::setOutput(true);
    M2_Sleep::setOutput(true);
    M1_Brake::setOutput(true); // BRAKE high: motor is braked.
    M2_Brake::setOutput(true);
    M1_Dir::setOutput(false);   // Direction doesn't matter here.
    M2_Dir::setOutput(false);
    driveForward(speedPercent);
    MODM_LOG_INFO << "br" << modm::endl; // "Rotate wheel manually; motor should not turn (brake active)."
    modm::delay_ms(testDuration_ms);

    // Test 4: Sleep Mode
    MODM_LOG_INFO << "04" << modm::endl; // "Test 4: Sleep Mode (nSLEEP=LOW, BRAKE=LOW, DIR=LOW)"
    M1_Sleep::setOutput(false); // nSLEEP low: driver in sleep.
    M2_Sleep::setOutput(false);
    M1_Brake::setOutput(false);
    M2_Brake::setOutput(false);
    M1_Dir::setOutput(false);
    M2_Dir::setOutput(false);
    driveForward(speedPercent);
    MODM_LOG_INFO << "sl" << modm::endl; // "Rotate wheel manually; motor should not run (sleep mode)."
    modm::delay_ms(testDuration_ms);
}

/**
 * @brief Main function.
 *
 * Initializes the board, performs a baseline drive test, then cycles through
 * enable combinations with manual rotation.
 */
int main()
{
    Board::initialize();
    MODM_LOG_INFO << "In" << modm::endl; // "Init."

    // Blink a heartbeat LED during startup.
    for (int i = 0; i < 5; i++) {
        Led_D2::toggle();
        modm::delay_ms(1000);
    }

    MODM_LOG_INFO << "75" << modm::endl; // "Starting baseline drive at 75% duty."
    modm::delay_ms(100);
    driveForward(75);
    modm::delay_ms(2000);

    // Run the enable mode tests.
    testEnableModes(50);

    MODM_LOG_INFO << "00" << modm::endl; // "End of tests."

    // After testing, continue with a heartbeat loop.
    while (true) {
        Led_D2::toggle();
        modm::delay_ms(1000);
    }

    return 0;
}

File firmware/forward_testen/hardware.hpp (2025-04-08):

#ifndef HARDWARE_HPP
#define HARDWARE_HPP

#include <modm/platform.hpp>
#include <modm/architecture/interface/clock.hpp>
#include <modm/platform/i2c/i2c_master_1.hpp>
#include <modm/platform/uart/uart_hal_1.hpp>

#include <modm/platform/timer/timer_3.hpp>
#include <modm/platform/timer/timer_2.hpp>


using namespace modm::platform;

namespace Board
{
    using namespace modm::literals;

    /// STM32G474 running at 170MHz from 16MHz internal clock
    struct SystemClock
    {
        static constexpr uint32_t Frequency = 170_MHz;
        static constexpr uint32_t Ahb1      = Frequency;
        static constexpr uint32_t Ahb2      = Frequency;
        static constexpr uint32_t Apb1      = Frequency;
        static constexpr uint32_t Apb2      = Frequency;

        static constexpr uint32_t Cordic    = Ahb1;
        static constexpr uint32_t Crc       = Ahb1;
        static constexpr uint32_t Dma       = Ahb1;
        static constexpr uint32_t Dma1      = Dma;
        static constexpr uint32_t Dma2      = Dma;
        static constexpr uint32_t DmaMux    = Dma;
        static constexpr uint32_t Fmac      = Ahb1;

        static constexpr uint32_t Adc       = Ahb2;
        static constexpr uint32_t Adc1      = Adc;
        static constexpr uint32_t Adc2      = Adc;
        static constexpr uint32_t Adc3      = Adc;
        static constexpr uint32_t Adc4      = Adc;
        static constexpr uint32_t Adc5      = Adc;
        static constexpr uint32_t Dac       = Ahb2;
        static constexpr uint32_t Dac1      = Dac;
        static constexpr uint32_t Dac2      = Dac;
        static constexpr uint32_t Dac3      = Dac;
        static constexpr uint32_t Dac4      = Dac;
        static constexpr uint32_t Rng       = Ahb2;

        static constexpr uint32_t Can       = Apb1;
        static constexpr uint32_t Fdcan1    = Can;
        static constexpr uint32_t Fdcan2    = Can;
        static constexpr uint32_t Fdcan3    = Can;
        static constexpr uint32_t I2c       = Apb1;
        static constexpr uint32_t I2c1      = I2c;
        static constexpr uint32_t I2c2      = I2c;
        static constexpr uint32_t I2c3      = I2c;
        static constexpr uint32_t I2c4      = I2c;
        static constexpr uint32_t Lptim     = Apb1;
        static constexpr uint32_t Lpuart    = Apb1;
        static constexpr uint32_t Rtc       = Apb1;
        static constexpr uint32_t Spi2      = Apb1;
        static constexpr uint32_t Spi3      = Apb1;
        static constexpr uint32_t Uart4     = Apb1;
        static constexpr uint32_t Uart5     = Apb1;
        static constexpr uint32_t Usart2    = Apb1;
        static constexpr uint32_t Usart3    = Apb1;
        static constexpr uint32_t Usb       = Apb1;
        static constexpr uint32_t Apb1Timer = Apb1 * 1;
        static constexpr uint32_t Timer2    = Apb1Timer;
        static constexpr uint32_t Timer3    = Apb1Timer;
        static constexpr uint32_t Timer4    = Apb1Timer;
        static constexpr uint32_t Timer5    = Apb1Timer;
        static constexpr uint32_t Timer6    = Apb1Timer;
        static constexpr uint32_t Timer7    = Apb1Timer;

        static constexpr uint32_t Sai1      = Apb2;
        static constexpr uint32_t Spi1      = Apb2;
        static constexpr uint32_t Usart1    = Apb2;
        static constexpr uint32_t Apb2Timer = Apb2 * 1;
        static constexpr uint32_t Timer1    = Apb2Timer;
        static constexpr uint32_t Timer8    = Apb2Timer;
        static constexpr uint32_t Timer15   = Apb2Timer;
        static constexpr uint32_t Timer16   = Apb2Timer;
        static constexpr uint32_t Timer17   = Apb2Timer;
        static constexpr uint32_t Timer20   = Apb2Timer;
        static constexpr uint32_t Iwdg = Rcc::LsiFrequency;


        static bool inline enable() {
            Rcc::enableInternalClock();    // 16MHz

            Rcc::PllFactors pllFactors
            {
                .pllM = 4,    //  16MHz / M= 4 ->   4MHz
                .pllN = 85,    //   4MHz * N=85 -> 340MHz
                .pllR = 2,    // 340MHz / R= 2 -> 170MHz = F_cpu
            };

            Rcc::enablePll(Rcc::PllSource::InternalClock, pllFactors);
            Rcc::setFlashLatency<Frequency>();
            Rcc::setVoltageScaling(Rcc::VoltageScaling::Boost); // recommended for >150 MHz
            // switch system clock to PLL output
            Rcc::enableSystemClock(Rcc::SystemClockSource::Pll);
            Rcc::setAhbPrescaler(Rcc::AhbPrescaler::Div1);
            // APB1 has max. 170MHz
            Rcc::setApb1Prescaler(Rcc::Apb1Prescaler::Div1);
            Rcc::setApb2Prescaler(Rcc::Apb2Prescaler::Div1);
            // update frequencies for busy-wait delay functions
            Rcc::updateCoreFrequency<Frequency>();

            Rcc::setCanClockSource(Rcc::CanClockSource::Pclk);
            return true;
        }
    };
    

    // ------------------- Led Pin -------------------
    using Led_D2 = GpioA11; //heartbeat led
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

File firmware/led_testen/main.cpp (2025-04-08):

/*
 * Copyright (c) 2024, Raphael Lehmann
 *
 * This file is part of the RCA project.
 *
 * This Source Code Form is subject to the terms of the Mozilla Public
 * License, v. 2.0. If a copy of the MPL was not distributed with this
 * file, You can obtain one at http://mozilla.org/MPL/2.0/.
 */

#include <modm/platform.hpp> //MODM platform library for GPIO and peripheral abstractions.
#include <modm/processing.hpp> //Includes lightweight threading support 
#include <modm/driver/position/vl53l0.hpp>
#include <modm/debug/logger.hpp> //to output debugging information over UART.

#include <type_traits>

#include "hardware.hpp" //hardware-specific configurations (e.g., clock, GPIO pins like GpioA0 for LEDs).

using namespace std::chrono_literals;

//A lightweight thread running independently of the main thread.
modm_faststack modm::Fiber<> fiber_blink([](){
    while (1) {
        Board::Led_D2::toggle();
        MODM_LOG_INFO << "Blink" << modm::endl; //Logs a “Blink” message via UART.
        modm::this_fiber::sleep_for(1s);
    }
});

int main()
{
    Board::initialize(); // Initialize system clock and GPIO pins.
//    Board::I2c::initialize(); // Initialize I2C peripheral.
    Board::DebugUart::initialize(); // Initialize UART for debugging.

    modm::fiber::Scheduler::run(); // Run the fiber scheduler (manages fibers).

    while(1) ; // Infinite loop (not reached since the fiber scheduler runs continuously).
    return 0;
}
